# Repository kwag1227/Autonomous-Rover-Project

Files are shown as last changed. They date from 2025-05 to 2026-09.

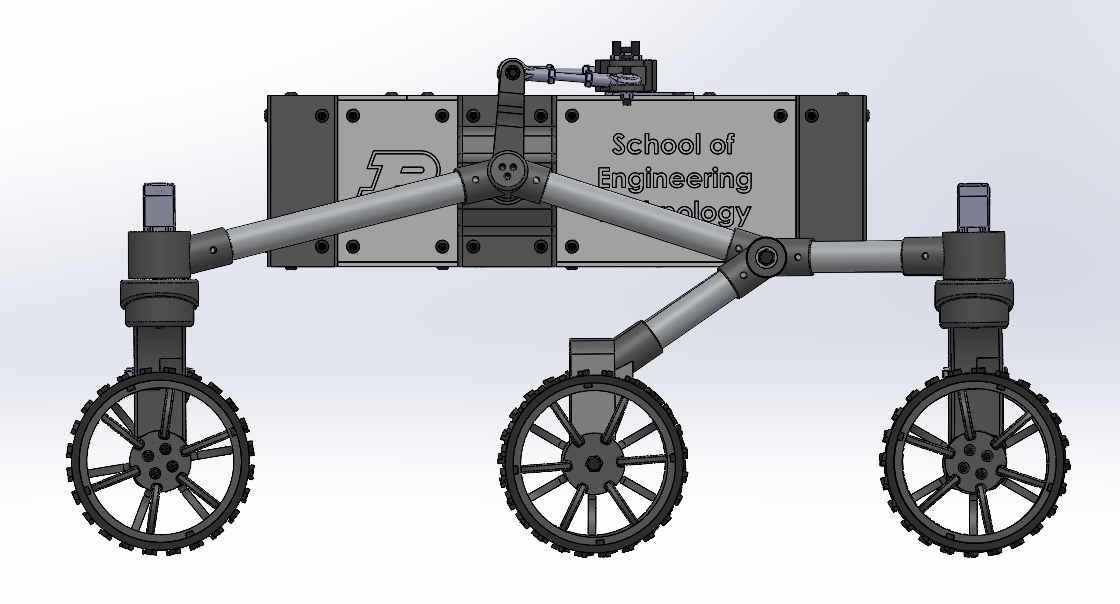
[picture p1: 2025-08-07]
mechanical designs/Screenshots/Screenshot 2025-08-07 133648.png

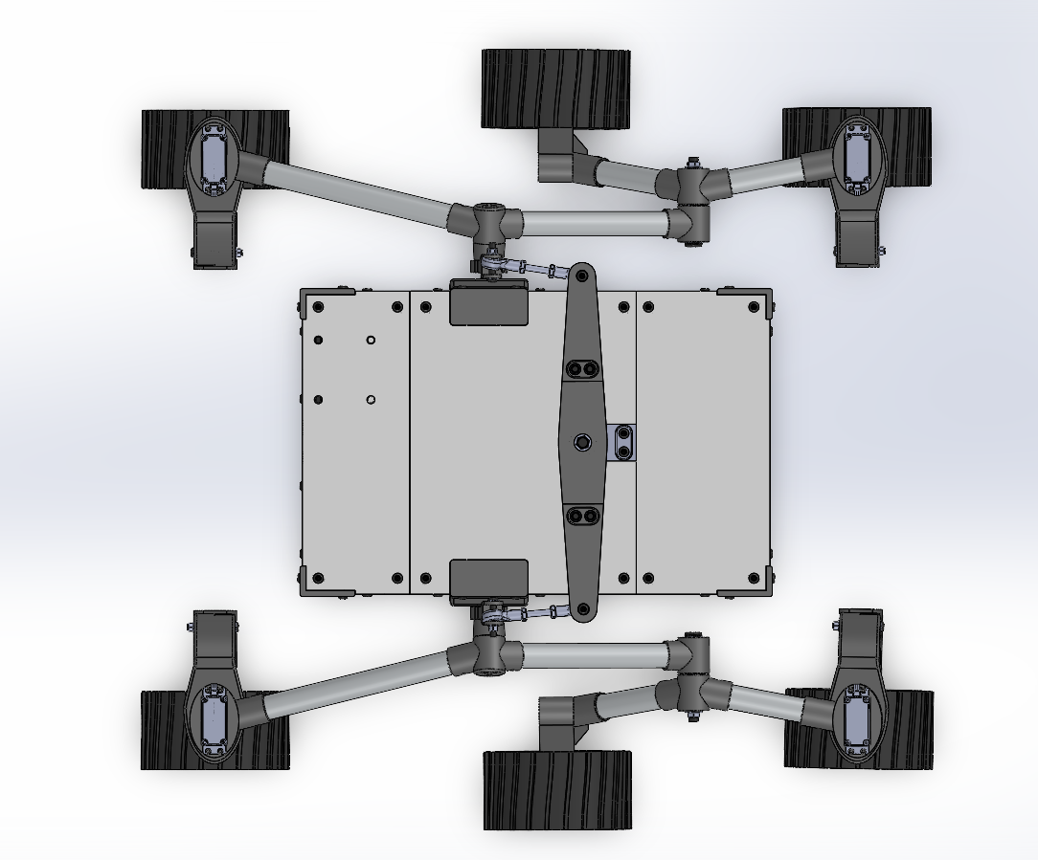
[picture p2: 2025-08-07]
mechanical designs/Screenshots/Screenshot 2025-08-07 133636.png

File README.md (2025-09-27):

# Autonomous Rover Project

This repository contains all design files, software, and documentation for an all-terrain, six-legged rover capable of navigating rough terrain and collecting environmental samples. It is a personal robotics project focused on demonstrating skills in embedded systems, motor control, and computer vision.

## 🚀 Project Goals

- Navigate difficult terrain using a rocker-bogie suspension system
- Collect and store small samples (e.g., rocks or soil)
- Avoid untraversable obstacles using sensors
- Showcase design and control of a multi-motor robotic system
- Build a custom PCB
- Implement ROS2 and Gazebo Simulation

## 📁 Repository Structure

- /code                       Microcontroller firmware and Raspberry Pi software  
- /mechanical design          CAD files & mechanical designs
- /electrical schematics      PCB schematics & electrical diagrams
- /vision                     Computer vision and object detection scripts  
- /docs                       Design notes and planning documents 
- /tests                      Testing scripts and logs  
- /media                      Images or videos of the rover in progress
- /references                 Reference images that I gathered from online
- /archives                   Outdated documents/files that are no longer in use
- README.md                   Project overview and documentation  

## 🧰 Technologies Used

- Raspberry Pi 4 (with OpenCV for computer vision)
- Raspberry Pi Pico
- Python Programming Language and ROS
- Rocker-Bogie Suspension System
- Camera Module
- Sensors (IMU, GPS, Encoders, Magnetometer)
- Custom PCB

## 🛠️ Current Progress

- [x] Preliminary Research
- [x] Conceptual Design
- [x] Power Distribution Design
- [x] Control/Communication Design
- [x] Master Electrical Schematic Design
- [x] PCB Design
- [x] CAD Design
- [x] Finalized BOM
- [x] Mechanical Assembly
- [ ] Electrical Assembly
- [ ] Basic Drive Logic
- [ ] Autonomy Logic
- [ ] Articulated Arm Design
- [ ] Articulation Logic 

## 📷 Media

*Add photos or videos here later*

## 🔒 Status

This is a personal project still under development

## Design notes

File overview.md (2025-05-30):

# All-Terrain Sampling Rover Project

## 1. Define Mission Requirements

### a. What is the goal?
The goal of this project is to create a rover-like robot that has similar functionality to real-life rovers used today, albeit on a much simpler scale. I plan to add to this project over time, learning about advanced features related to computer vision and robot navigation eventually.

### b. What are the operational constraints?

#### i. Mechanical:
- Collect 10mL sample and store
- Traversable across rocky/uneven terrain

#### ii. Electrical:
- Minimum runtime of 15 minutes
- Wireless operation
- Solar-rechargeable battery

#### iii. Software:
- Autonomous control – Finite State Machine
- Sensor feedback (IMU, Camera, Ultrasonic Sensor, Wheel Encoders)
- Decision-making based on I/O
- GPS tracking
- Implement ROS

---

## 2. Subsystem Breakdown

### a. Chassis
- **Purpose**: Houses majority of electronics and hardware, provides protection against outside elements  
- **Function**: Shield electronics, maintain upright position, hold inner contents securely  
- **Components**: Frame, housings, internal/external mounts  

### b. Drivetrain
- **Purpose**: High-torque system that allows for movement on steep inclines  
- **Function**: Forward/backward movement, differential drive, steering capability  
- **Components**: 4x Wheel motors (BLDC), high-grip wheels, leg assemblies, wire housing  

### c. Power System
- **Purpose**: Providing power to all components  
- **Function**: Voltage regulation, current protection, battery management, stepping down voltage for logic devices, on/off control  
- **Components**: Battery pack, on/off switch, 12V-to-5V buck converter, fuse/current limiter, ground bus, microcontroller breakout board, PCB board  

### d. Control
- **Purpose**: Managing I/O and coordinating robot functions  
- **Function**: Generating PWM signals, processing remote control inputs, managing sensor data, using logic to make decisions  
- **Components**: Main Controller (Raspberry Pi 3 – Arduino Mega doesn’t support camera), Drive ESCs, Articulated Arm Controller (Pi Pico)  

### e. Sensing
- **Purpose**: Measuring and recording data for decision-making  
- **Function**: Track robot position/orientation, detect obstacles, track state of sample collector  
- **Components**: Ultrasonic sensor, IMU, camera module, wheel encoders  

### f. Actuation
- **Purpose**: Controlling the sample-collecting device  
- **Function**: Using a 2–3 DOF articulated arm for scooping  
- **Components**: 1 main arm link, 3 servo motors (base rotation, shoulder hinge, wrist hinge – high torque), end effector (scooper)  

### g. Communications
- **Purpose**: Data transfer between subsystems  
- **Function**: Sensor/controller communication, command output, code uploading  
- **Components**: UART/I2C/SPI buses, USB/Ethernet (for code uploading)  

---

## 3. Performance Specs

### Chassis
- **Max weight capacity**: ≥ 18 lbs

### Drivetrain
- **Max obstacle height**: 150% of Wheel Diameter (6.75")
- **Minimum drive motor torque**: 17.7 in-lbs (2.0 N*m)

### Power System
- **Battery life**: ≥ 15 minutes continuous operation
- **Voltage rails**: 12V, 5V
- **Safety**: Include overcurrent protection and emergency shutoff

### Control
- **Latency (input to actuation)**: ≤ 100 ms
- **Redundancy**: Safe failure behavior if primary controller fails
- **Interface compatibility**: Must support all communication protocols

### Sensing
- **Obstacle detection range (ultrasonic)**: ≥ 5'
- **IMU update rate**: ≥ 100 Hz
- **Camera resolution**: ≥ 640x480 @ 30 fps
- **Sensor fusion accuracy**: ≤ ±5° orientation error

### Actuation (Sampler Device)
- **Reach**: ≥ 10" from arm base
- **Payload capacity**: ≥ 3lbs (soil or rock sample)
- **Servo torque**: Sufficient to operate at full arm extension under load
- **Repeatability**: ≤ 0.5" positioning error
- **Degrees of Freedom**: 3

### Communications
- **Internal latency (inter-microcontroller)**: ≤ 10 ms
- **Signal integrity**: Must operate reliably under EMI from motors
- **Wiring**: Clearly labeled, shielded where needed
- **Bandwidth**: Must support 30 fps camera feed to Pi 3
- **Protocol support**: WIFI UART, I2C, SPI, PWM

### Software
- **Error handling**: Subsystem-level watchdogs and fail-safe states
- **Modularity**: Software structured into independent modules for each subsystem
- **Real-time control loop**: ≥ 10 Hz for locomotion and sensing
- **Remote override**: Support for manual override during autonomous mode

---

## 4. Interfacing

### a. I2C
- **Benefits**: Only two wires to connect many components  
- **Usage**: Connecting sensors to the Pi  
- **Limitations**: Short-range, noise-prone, address conflicts, slow speed (not suitable for camera)  

### b. CSI
- **Benefits**: High data throughput, Pi-optimized, easy and power-efficient  
- **Usage**: Connecting camera module  
- **Limitations**: Limited number of ports, requires CSI-compatible camera  

### c. Wi-Fi
- **Usage**: Streaming camera feed/sensor data to laptop from Pi  

### d. PWM
- **Usage**: Controller output signal to ESCs and motors  

### e. UART
- **Benefits**: Only 2 lines, GPS-compatible, asynchronous  
- **Usage**: Communicating with GPS module  
- **Limitations**: One-to-one device connection, baud rate must match, code must read data quickly  

---

## 5. Documentation

- **BOM Link**: _[https://docs.google.com/spreadsheets/d/1kCPw5noG4wiGUhccGp7jNWA5f-jaydbZb4b8pzQ2dAw/edit?usp=sharing]_  
- **GitHub**: _[https://github.com/kwag1227/Autonomous-Rover-Project/tree/main]_  
- **YouTube Video Progress Reports**: _[Add playlist or links]_

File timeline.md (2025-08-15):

## Project Timeline

### Week 1 – Project Planning & Scoping
- Finalize project overview (mission, constraints, subsystems)
- Create early sketches of subsystems
- Set up documentation system (GitHub, folders)

### Week 2 – Conceptual Design
- Create master sketch with accurate dimensions
- Define conceptual control flow between sensors, logic, and motors
- Decide PCB responsibilities

### Week 3 – Detailed Design
- Finalize mechanical and control architecture
- Select core electrical components

### Week 4 – BOM Refinement & Electrical Schematics
- Swap general parts for specific parts
- Create power distribution PCB electrical schematic
- Create control PCB electrical schematic

### Week 5 – PCB Schematic Design
- Finish electrical components refinement
- Create KiCAD master electrical schematic for PCB
- Perform electronic rules check and address all errors/warnings

### Week 6 – PCB Layout Design
- Research PCB design principles
- Create PCB layout based off finalized electrical schematic
- Perform design rules check and address all errors/warnings

### Week 7 – Mechanical Design Kickoff
- Refine BOM for mechanical components
- Establish deadlines for mechanical subsystems
- Begin work on rover chassis

### Week 8 – Chassis Design + 3D Printer Order
- Order 3D Printer + Accessories
- Select 3D print materials for rover components
- Finish mechanical design of rover chassis

### Week 9 – Drivetrain Design & Filament Ordering
- Order all electrical components
- Design rocker-bogie drivetrain subsystem
- Set up 3D printer and order required filaments types

### Week 10 – CAD Finalization, Parts Ordering, Pi 4 Setup
- Finalize CAD model
- Order MCUs + accessories and PCB + components for soldering
- Set up Raspberry OS on Pi 4

### Week 11 – BOM Finalization, Software Setup & Training
- Finalize BOM with updated mechanical components
- Solder all PCB components
- Set up Pi Pico
- Install ROS2 and Gazebo software
- C++ and ROS2 Training

### Week 12 – Project Relocation / Transition Week
- Moving back to university, bring all required components and equipment
- Begin printing drivetrain components
- Order mechanical components if possible

### Week 13 & Beyond - Electrical and Mechanical Assembly
- Order/print all remaining components and assemble
- Finish internal/external wiring
- Begin writing ROS2 nodes for rover locomotion
- Create project overview video

### Future Additions - Advanced logic scripts + rover functionality
- Implement logic that handles all sensor data and provides live telemetry to off-board computer
- Create FSM-level autonomy logic.
- Begin implementing Gazebo simulation
- Design and implement 3-axis robotic arm for sample gathering
- Finish 2-DOF camera mount design
- Consider future additions (actuated camera head, SLAM computer vision, & sample storage)

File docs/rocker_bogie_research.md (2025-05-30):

# Rocker-Bogie Drivetrain Research

## Overview
Below is notes taken regarding the rocker-bogie suspension system that will be used for this project. 
This is a preliminary document intended for future reference during the design phase.
Created on 5/20/25

## Mechanical Design
- 3 Main Components:
    1. Differential - Pivot point about center of chassis, connects left and right rockers to the rover body. Acts as a counter-balancing mechanism (one rocker goes up, the other goes down), keeping the chassis more level and all wheels in contact with the ground. Can be done using bevel gears, but NASA opts for a pivoting mechanical linkage, which reduces points of failure.
    2. Rocker - Main joint that connects the front wheel to the bogie. The rocker linkage connector is fastened to the joint hub, and the joint hub rotates around a fixed shaft protruding from the chassis. See reference images for joint hub design.
    3. Bogie - Secondary rocker that connects the middle and back wheels together.
- This design provides fully passive stability, there are no springs that maintain a default position.

## Kinematics & Geometry
- For both the rocker and bogie, the links on each side are the same length. This means that the middle wheels are shifted closer to the back wheels than to the front wheel.
- Wheels can traverse obstacles 1.5-2 * wheel diameter
- Can handle 45 degree tilt in any direction
- Front and back wheels are aligned, middle wheels stick out about half a wheel more

## Materials and Components
- All of the weight of the rocker-bogie suspension will be on the rocker joint hub components, which should be made of a stronger material.
- All components are stiff and a fixed size besides the wheel tread, which should be slightly pliable and have a tread pattern of simple horizontal lines.

## Design Considerations for My Rover
- I should probably use the same differential system used by NASA, which will be easier to 3d print. An additional linkage is required on each side with this version. This linkage is connected via two pinned joints, allowing for the linkage to remain forward-facing despite the transverse-plane rotation of the differential bar and sagittal-plane rotation of the rocker joint hub.
- While NASA utilizes four steering motors (one for each corner), I only need to use two for the front two wheels. Use Ackermann steering calculations to independently control the angle of each wheel during a turn. Include motor hubs for back wheels in case want more manuevarability in future.
- The sides are mirrors of each other, don't make them identical.
- The rocker joint component, on which the rocker linkage connection is fastened, is tilted slightly upwards, which is what allows for the linkages to go outwards at an angle, rather than being straight up and down.
- Dimensions (given in mm) have been uploaded to reference images folder, decide what scale you want to use for this and convert values from there. Keep in mind that the values used in the the reference image dimensions are not the same scale as the real rover, but they are proportionally accurate.
- Make sure that the rocker joint 3d-printed component is printed with the layers travelling along the shaft that the links are fastened too. That area us under the most stress due to it holding the full weight of the chassis.

## References
NASA JPL Youtube Video - https://www.youtube.com/watch?v=BC441bV1wFc
NASA Website Perserverance Rover Breakdown - https://science.nasa.gov/mission/mars-2020-perseverance/rover-components/
DIY Rover Youtube Video - https://www.youtube.com/watch?v=NOZZMsMAGh0&t=1s
NASA-provided 3D Model - https://science.nasa.gov/resource/mars-perseverance-rover-3d-model/
Check reference images folder

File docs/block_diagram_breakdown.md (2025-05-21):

# Autonomous Rover Project – High-Level System Block Diagram

## 📦 Subsystem Breakdown

### 1. Chassis
**Components:**
- Frame
- Top and bottom plates
- Side plates
- Front and back plates
- Battery housing
- Internal/external mounts

---

### 2. Drivetrain
**Components:**
- 4x BLDC drive motors
- 2x High-torque servo motors (for steering)
- High-grip, flexible wheels
- Wheel hubs
- Rocker-bogie assembly
- Differential bar assembly

---

### 3. Power System
**Components:**
- LiPo battery
- Battery connector (XT90)
- DC On/off switch
- 12V-5V Buck converter
- Screw terminals
- Fuse/breaker
- Ground bus
- Power PCB board
- Wire hose
- Zip ties

---

### 4. Control
**Components:**
- Main Controller: Raspberry Pi 3
- Robot Controller: Raspberry Pi Pico
- Main PCB Board
- Drive ESCs
- GPIO headers

---

### 5. Sensing
**Components:**
- Ultrasonic sensor
- IMU
- Camera module
- Wheel encoders
- Limit switches? (for arm)
- GPS?

---

### 6. Actuation 
**Components:**
- Main arm link
- Shoulder joint hub
- Wrist joint hub
- End effector (scooper)
- 3x Additional high-torque servo motors (shoulder rotation, shoulder hinge, wrist hinge)

---

### 7. Communications
**Components:**
- UART bus wiring/connectors
- UART twisted wire cables (TX+gnd, RX+gnd)
- I2C bus wiring/connectors
- I2C twisted wire cables (SDA+gnd, SCL+gnd)
- I2C pull-up resistors (For SDA and SCL lines)
- CSI ribbon cable
- PWM wires

---

## 🖼️ Block Diagram

**Diagram Filename:** `Rover Block Diagram.png`

_Description:_  
This diagram illustrates the connections and dependencies between all major subsystems, including power distribution, sensory input, decision-making, and actuation systems.

---

## 📌 Notes & Future Considerations

- Consider adding solar recharging or power monitoring sensors.
- Possible integration of SLAM or GPS for autonomous mapping in the future.
- Expand sensing array with LIDAR or stereo vision for better 3D awareness.

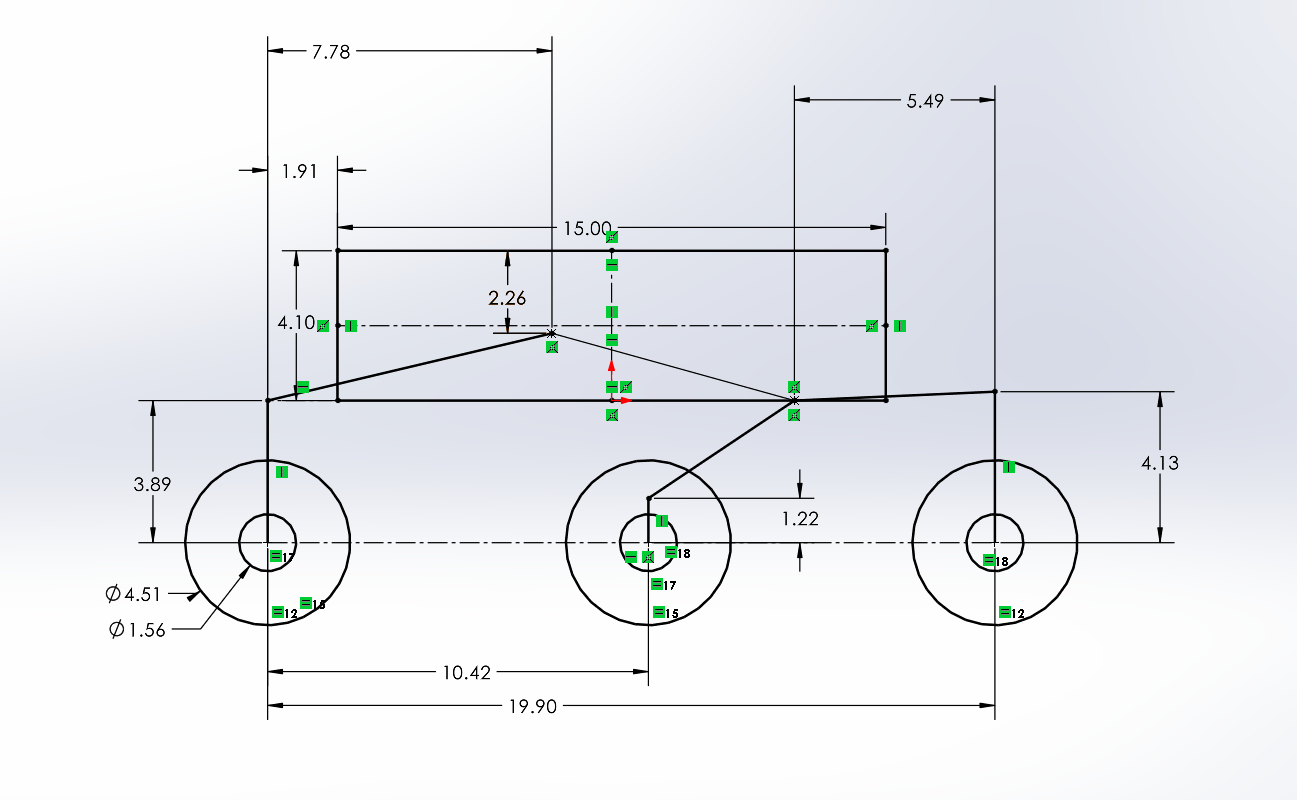
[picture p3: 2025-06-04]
mechanical designs/Screenshots/Master Sketch Side View Screenshot.png

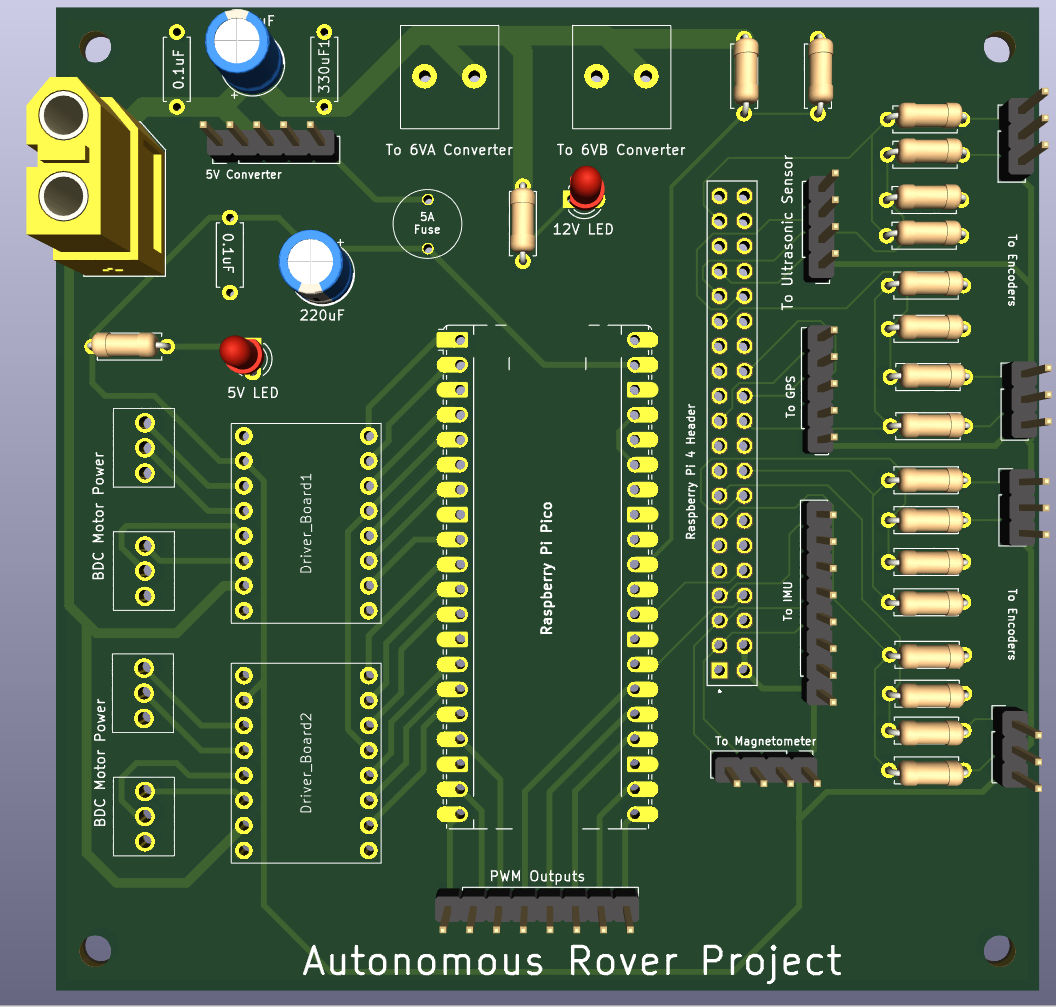
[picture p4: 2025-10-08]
electrical schematics/PCB 3D Viewer.png

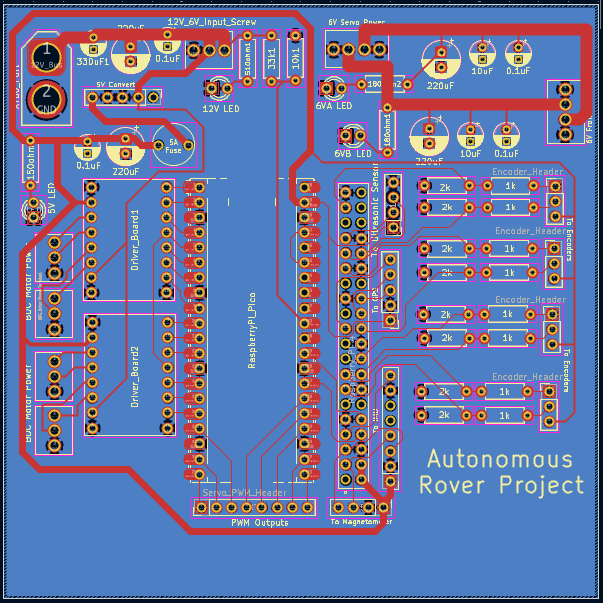
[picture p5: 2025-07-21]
electrical schematics/Finalized PCB Layout.png

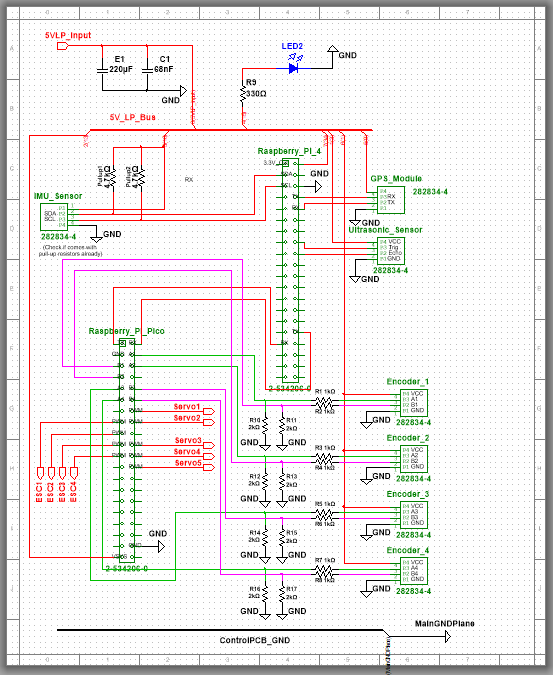
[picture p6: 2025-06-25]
electrical schematics/Control Schematic Screenshot.png

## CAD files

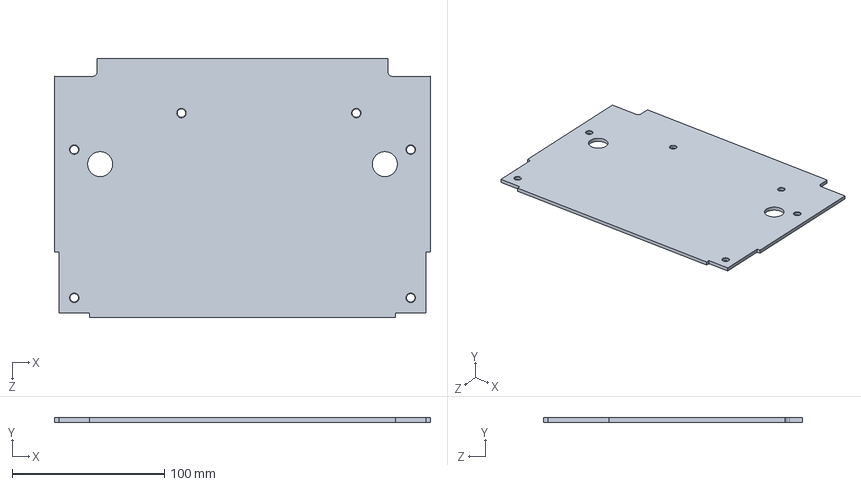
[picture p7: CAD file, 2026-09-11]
mechanical designs/Chassis/Top_Bottom_Panels.SLDPRT
247.3 x 3.00 x 170.5 mm

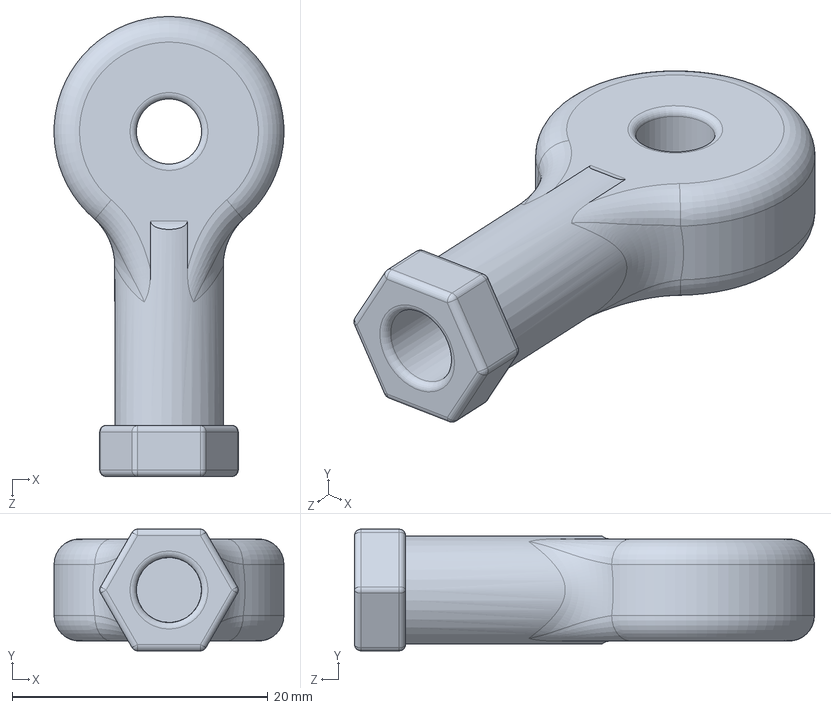
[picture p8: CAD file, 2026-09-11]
mechanical designs/Fasteners & Power Transmission/Heim Joint/Hiem Joint Socket.SLDPRT
18.0 x 9.53 x 36.0 mm

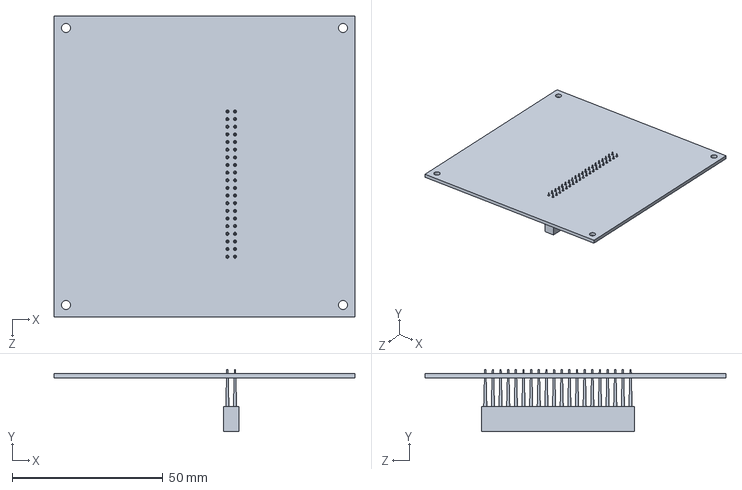
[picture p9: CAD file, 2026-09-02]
mechanical designs/Internal Electronics/PCB.SLDPRT
100.0 x 20.7 x 100.0 mm

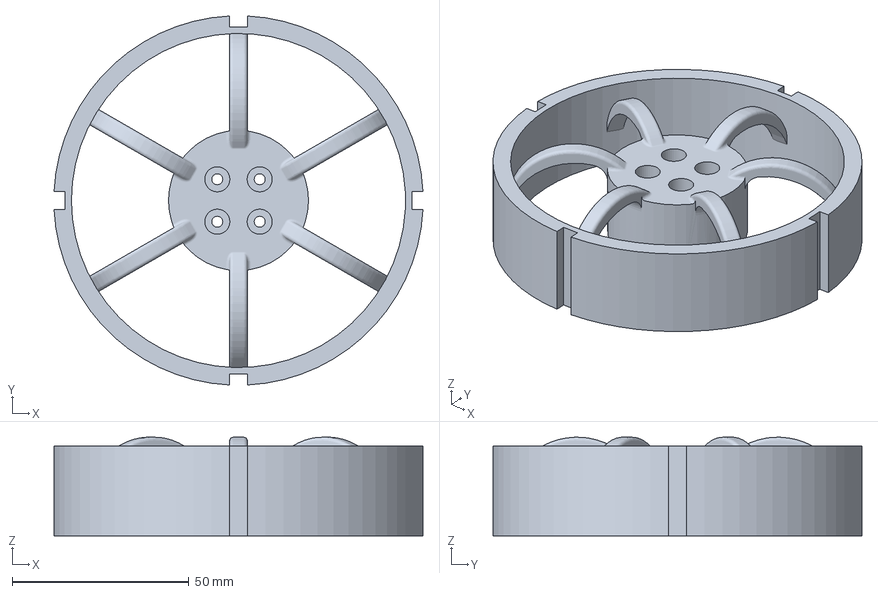
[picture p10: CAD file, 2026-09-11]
mechanical designs/Print Files/PETG White/Outer Wheel Hub.3mf
104.4 x 104.4 x 27.9 mm

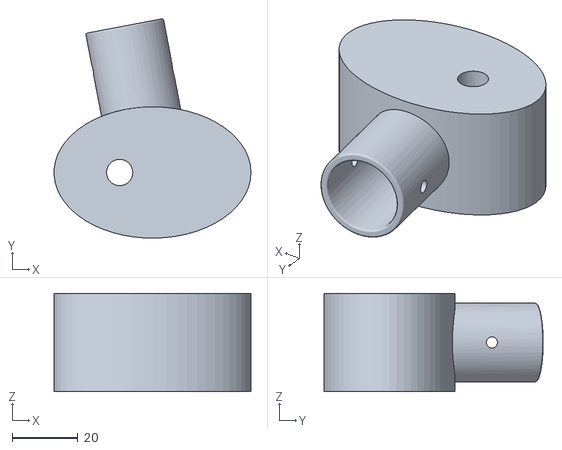
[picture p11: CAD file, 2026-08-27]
mechanical designs/Print Files/PETG-CF Gray/Steering Motor Housing Back Left.STL
60.0 x 66.8 x 30.0

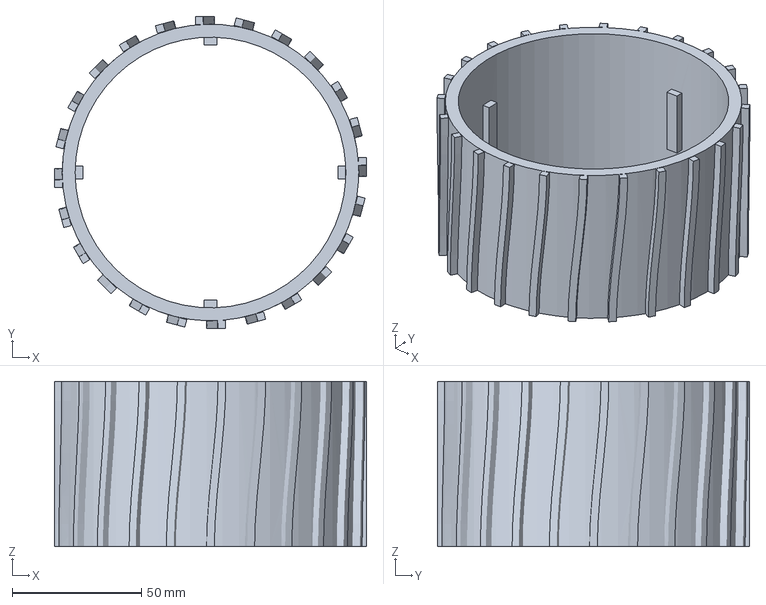
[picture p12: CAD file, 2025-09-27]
mechanical designs/Print Files/TPU 95A Black/Tires.3mf
120.5 x 120.5 x 63.8 mm

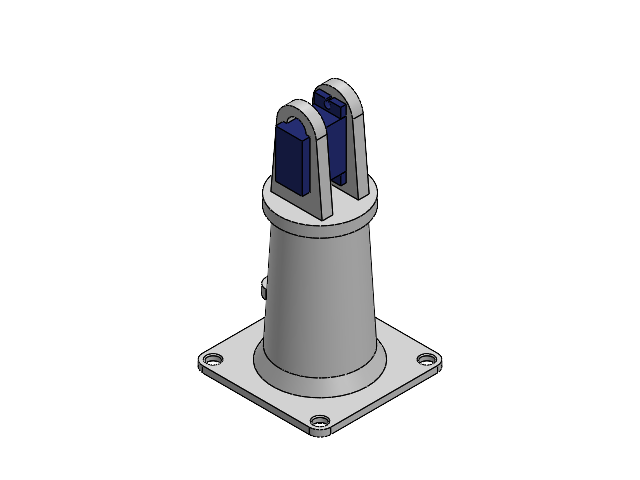
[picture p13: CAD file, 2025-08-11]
mechanical designs/Camera Head/Camera Mount Subassembly.SLDASM
Component1.step x 2
Component2.step x 2
Component3.step x 2
Component4.step x 2
Component5.step x 2
Component6.step x 2
Servo Shaft Coupler
Threaded Rod
Pitch Servo Mount
Camera Mount Base

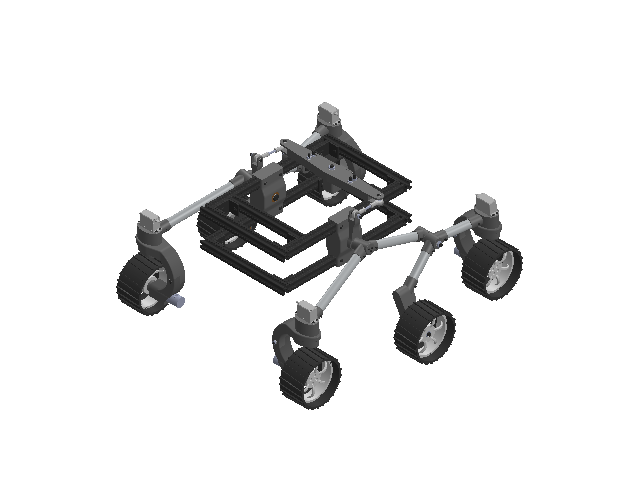
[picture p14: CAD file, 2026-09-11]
mechanical designs/Drivetrain/Drivetrain Subassembly.SLDASM
T-Slot_Extrusions x 10
T-Slot_Nut x 44
Threaded_Bolts x 149
T-Slot_Corner_Bracket x 12
Rocker_Joint_Mounting_Plate x 2
Ball_Bearing x 12
Differential_Mount
Differential Center Piece
Washers x 37
Nuts x 19
Differential Outer Piece x 2
Threaded Rods x 2
Rocker Joint Hub x 2
Hiem Joint Socket x 4
Hiem Joint Bearing x 4
Threaded Insert x 46
Rocker Joint x 2
20mm Aluminum Tubes x 8
Bogie Components x 4
SW2019 DS3225MG Servo 25Kg 4.8-6.8V x 4
Servo Horn x 4
Steering Motor Housing x 3
Steering Linkage x 4
Drive Motor x 4
Drive Motor Housing x 4
Middle Wheel Hub x 2
Drive Motor Shaft Coupler x 4
Wheel Hub x 6
Tires x 6

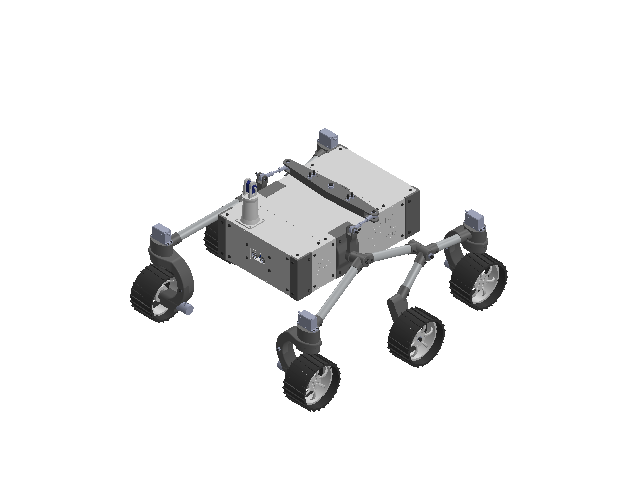
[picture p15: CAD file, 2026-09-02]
mechanical designs/Top Level Assembly.SLDASM
T-Slot_Extrusions x 10
T-Slot_Nut x 104
Threaded_Bolts x 221
T-Slot_Corner_Bracket x 12
Rocker_Joint_Mounting_Plate x 2
Ball_Bearing x 12
Chassis_Corner_Panel x 4
Side_Panels x 4
ultrasonic sensor_3.step
Ultrasonic_Sensor_Bracket
Chassis_Front_Panel x 2
Nuts x 23
Differential_Mount
Top_Bottom_Panels x 5
Battery
PCB, RPi4ModelB.step
Broadcom BCM2711B0 CPU, RPi4ModelB.step
2.54 mm DUPONT MALE PIN HEADER, POE, 2X2, RPi4ModelB.step
2.54 mm DUPONT MALE PIN HEADER, IO, 2X20, RPi4ModelB.step
Camera Connector, RPi4ModelB.step
Microphone Plug, RPi4ModelB.step
Display Connector, RPi4ModelB.step
Gigabit Ethernet Port, RPi4ModelB.step
Female Micro HDMI Connector, RPi4ModelB.step x 2
Female USB Type C Connector, RPi4ModelB.step
2X USB3.0 PORTS, RPi4ModelB.step
91D77 D9WHV 778K, 4 GB LPDDR4 SDRAM, RPi4ModelB.step
Cypress CYW43455 Wireless Module Cover, RPi4ModelB.step
SD Card Slot, RPi4ModelB.step
VIA VL805 PCIe USB 3.0 controller, RPi4ModelB.step
2X USB2.0 PORTS, RPi4ModelB.step
Broadcom BCM54213PE Gigabit Ethernet Transceiver, RPi4ModelB.step
MxL7704 Universal PMIC, RPi4ModelB.step
PCB
MCU-PCB Mounting Plate^MCU-PCB Mounting Plate
Differential Center Piece
Washers x 42
Differential Outer Piece x 2
Threaded Rods x 2
Rocker Joint Hub x 2
Hiem Joint Socket x 4
Hiem Joint Bearing x 4
Threaded Insert x 30
Rocker Joint x 2
20mm Aluminum Tubes x 8
Bogie Components x 4
SW2019 DS3225MG Servo 25Kg 4.8-6.8V x 4
Servo Horn x 4
Servo Horn Coupler x 4
Steering Motor Housing
Steering Linkage x 4
Drive Motor x 4
Drive Motor Housing x 4
Middle Wheel Hub x 2
Drive Motor Shaft Coupler x 4
Wheel Hub x 6
Tires x 6
Component1.step x 2
Component2.step x 2
Component3.step x 2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

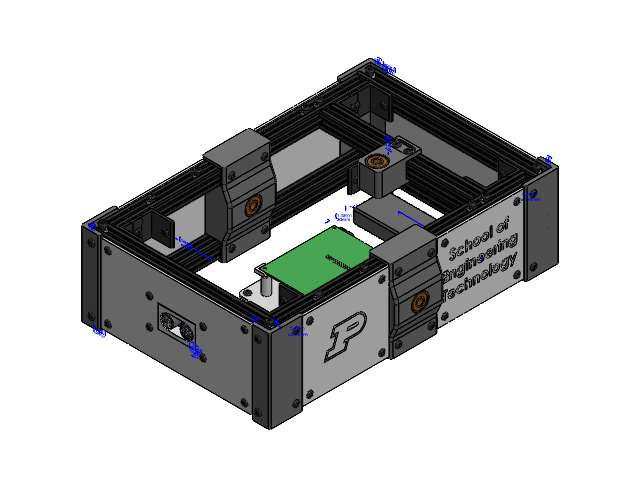
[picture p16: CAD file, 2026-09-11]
mechanical designs/Chassis/Chassis_Subassembly.SLDASM
T-Slot_Extrusions x 9
T-Slot_Nut x 104
Threaded_Bolts x 116
T-Slot_Corner_Bracket x 12
Rocker_Joint_Mounting_Plate x 2
Ball_Bearing x 6
Chassis_Corner_Panel x 4
Side_Panels x 4
ultrasonic sensor_3.step
Ultrasonic_Sensor_Bracket
Chassis_Front_Panel x 2
Nuts x 8
Differential_Mount
Battery
PCB, RPi4ModelB.step
Broadcom BCM2711B0 CPU, RPi4ModelB.step
2.54 mm DUPONT MALE PIN HEADER, POE, 2X2, RPi4ModelB.step
2.54 mm DUPONT MALE PIN HEADER, IO, 2X20, RPi4ModelB.step
Camera Connector, RPi4ModelB.step
Microphone Plug, RPi4ModelB.step
Display Connector, RPi4ModelB.step
Gigabit Ethernet Port, RPi4ModelB.step
Female Micro HDMI Connector, RPi4ModelB.step x 2
Female USB Type C Connector, RPi4ModelB.step
2X USB3.0 PORTS, RPi4ModelB.step
91D77 D9WHV 778K, 4 GB LPDDR4 SDRAM, RPi4ModelB.step
Cypress CYW43455 Wireless Module Cover, RPi4ModelB.step
SD Card Slot, RPi4ModelB.step
VIA VL805 PCIe USB 3.0 controller, RPi4ModelB.step
2X USB2.0 PORTS, RPi4ModelB.step
Broadcom BCM54213PE Gigabit Ethernet Transceiver, RPi4ModelB.step
MxL7704 Universal PMIC, RPi4ModelB.step
PCB
MCU-PCB Mounting Plate^MCU-PCB Mounting Plate

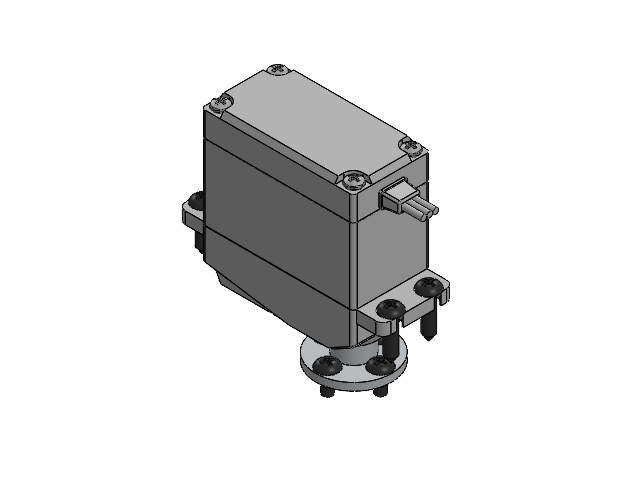
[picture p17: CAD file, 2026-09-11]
mechanical designs/Drivetrain/Steering Motor Mount.SLDASM
SW2019 DS3225MG Servo 25Kg 4.8-6.8V
Servo Horn
Threaded_Bolts x 8

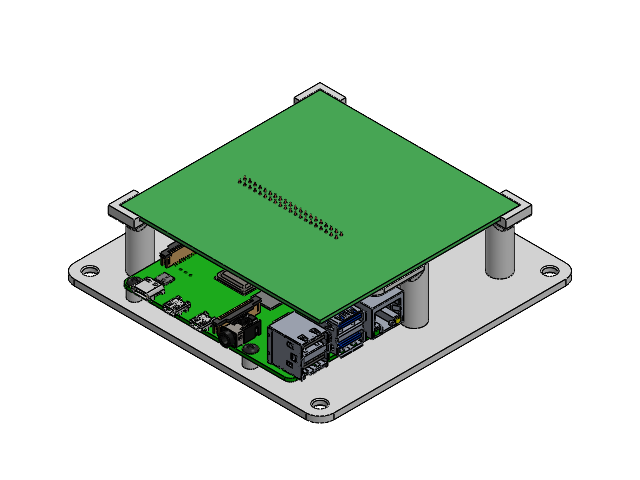
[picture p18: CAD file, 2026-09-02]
mechanical designs/Internal Electronics/MCU-PCB Mounting Plate.SLDASM
PCB, RPi4ModelB.step
Broadcom BCM2711B0 CPU, RPi4ModelB.step
2.54 mm DUPONT MALE PIN HEADER, POE, 2X2, RPi4ModelB.step
2.54 mm DUPONT MALE PIN HEADER, IO, 2X20, RPi4ModelB.step
Camera Connector, RPi4ModelB.step
Microphone Plug, RPi4ModelB.step
Display Connector, RPi4ModelB.step
Gigabit Ethernet Port, RPi4ModelB.step
Female Micro HDMI Connector, RPi4ModelB.step x 2
Female USB Type C Connector, RPi4ModelB.step
2X USB3.0 PORTS, RPi4ModelB.step
91D77 D9WHV 778K, 4 GB LPDDR4 SDRAM, RPi4ModelB.step
Cypress CYW43455 Wireless Module Cover, RPi4ModelB.step
SD Card Slot, RPi4ModelB.step
VIA VL805 PCIe USB 3.0 controller, RPi4ModelB.step
2X USB2.0 PORTS, RPi4ModelB.step
Broadcom BCM54213PE Gigabit Ethernet Transceiver, RPi4ModelB.step
MxL7704 Universal PMIC, RPi4ModelB.step
PCB
MCU-PCB Mounting Plate^MCU-PCB Mounting Plate
Threaded_Bolts x 4

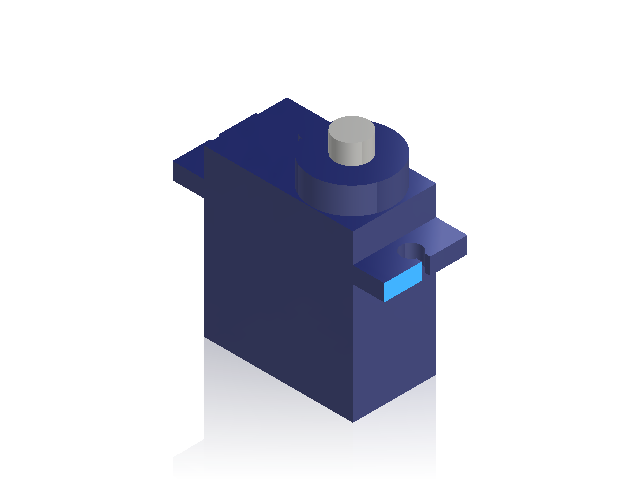
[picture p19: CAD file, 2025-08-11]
mechanical designs/Camera Head/SG90 Servo Beffkipp.SLDASM
Component1.step
Component2.step
Component3.step
Component4.step
Component5.step
Component6.step

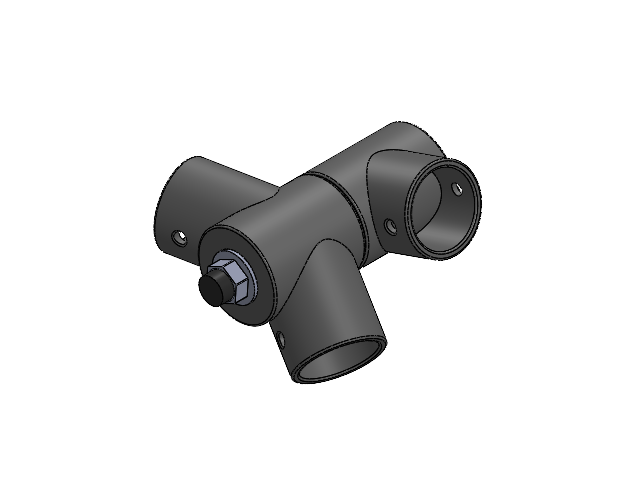
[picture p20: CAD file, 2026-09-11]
mechanical designs/Drivetrain/Bogie Joint.SLDASM
Ball_Bearing x 2
Nuts
Threaded_Bolts
Washers x 3
Bogie Components x 2

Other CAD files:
mechanical designs/Fasteners & Power Transmission/Heim Joint/Female Heim Joint.SLDASM
mechanical designs/Chassis/Corner_Bracket_Subassembly.SLDASM
mechanical designs/Drivetrain/Drive Motor Joint.SLDASM
mechanical designs/Drivetrain/Wheel Assembly.SLDASM
mechanical designs/Camera Head/Camera Mount Base.SLDPRT
mechanical designs/Camera Head/Pitch Servo Mount.SLDPRT
mechanical designs/Camera Head/Servo Shaft Coupler.SLDPRT
mechanical designs/Camera Head/Threaded Rod.SLDPRT
mechanical designs/Chassis/Chassis_Corner_Panel.SLDPRT
mechanical designs/Chassis/Chassis_Front_Panel.SLDPRT
mechanical designs/Chassis/Differential_Mount.SLDPRT
mechanical designs/Chassis/Rocker_Joint_Mounting_Plate.SLDPRT
mechanical designs/Chassis/Side_Panels.SLDPRT
mechanical designs/Chassis/T-Slot_Extrusions.SLDPRT
mechanical designs/Chassis/Ultrasonic_Sensor_Bracket.SLDPRT
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

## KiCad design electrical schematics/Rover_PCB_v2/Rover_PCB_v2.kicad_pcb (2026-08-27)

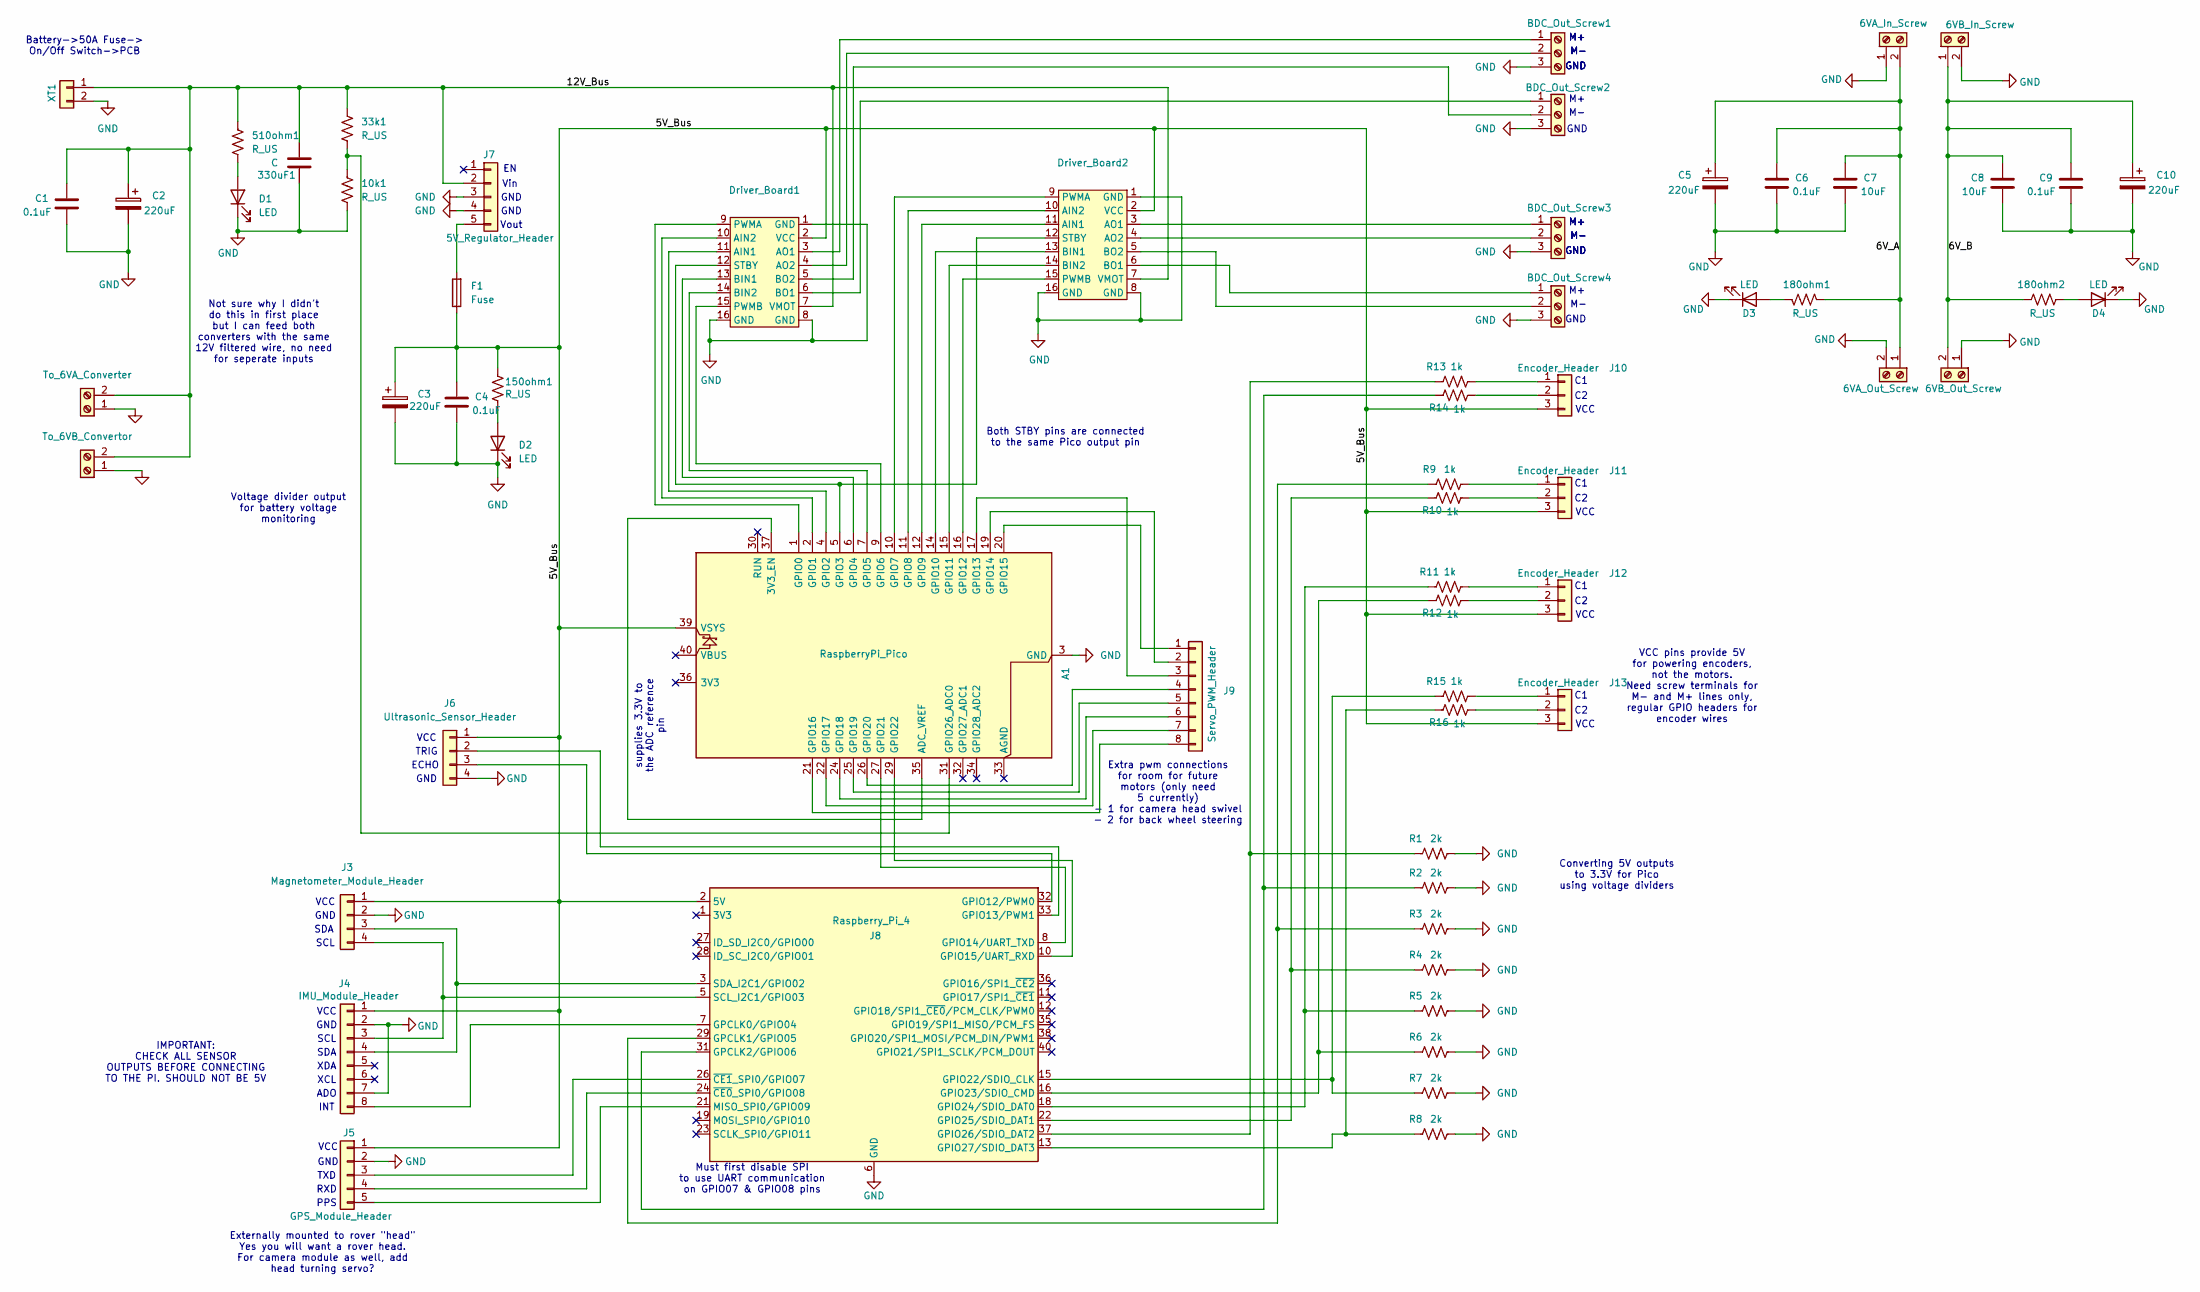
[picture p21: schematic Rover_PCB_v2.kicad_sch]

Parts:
10k1, 33k1, 150ohm1, 180ohm1, 180ohm2, 510ohm1: R_US; R_Axial_DIN0207_L6.3mm_D2.5mm_P7.62mm_Horizontal
330uF1: C; CP_Radial_D4.0mm_P2.00mm
A1: RaspberryPi_Pico; RaspberryPi_Pico_Common_Unspecified
BDC_Out_Screw1, BDC_Out_Screw2, BDC_Out_Screw3, BDC_Out_Screw4: BDC_Motor_Screw_Terminal; 01x03_Screw_Terminal
C1, C4, C6, C9: 0.1uF; CP_Radial_D4.0mm_P2.00mm
C2, C3, C5, C10: 220uF; CP_Radial_D6.3mm_P2.50mm
C7, C8: 10uF; CP_Radial_D4.0mm_P2.00mm
D1, D2, D3, D4: LED; LED_D3.0mm
Driver_Board1, Driver_Board2: Motor Driver Board
F1: Fuse; Fuse_TH_5A
J1: To_6VA_Converter; 12AWG Screw Terminal
J2: To_6VB_Convertor; 12AWG Screw Terminal
J3: Magnetometer_Module_Header; PinHeader_1x04_P2.54mm_Vertical
J4: IMU_Module_Header; PinHeader_1x08_P2.54mm_Vertical
J5: GPS_Module_Header; PinHeader_1x05_P2.54mm_Vertical
J6: Ultrasonic_Sensor_Header; PinHeader_1x04_P2.54mm_Vertical
J7: 5V_Regulator_Header; PinHeader_1x05_P2.54mm_Vertical
J8: Raspberry_Pi_4; SULLINS_PPTC202LFBN-RC
J9: Servo_PWM_Header; PinHeader_1x08_P2.54mm_Vertical
J10, J11, J12, J13: Encoder_Header; PinHeader_1x03_P2.54mm_Vertical
J14: 6VA_In_Screw; 12AWG Screw Terminal
J15: 6VA_Out_Screw; 12AWG Screw Terminal
J16: 6VB_In_Screw; 12AWG Screw Terminal
J17: 6VB_Out_Screw; 12AWG Screw Terminal
R1, R2, R3, R4, R5, R6, R7, R8: 2k; R_Axial_DIN0207_L6.3mm_D2.5mm_P7.62mm_Horizontal
R9, R10, R11, R12, R13, R14, R15, R16: 1k; R_Axial_DIN0207_L6.3mm_D2.5mm_P7.62mm_Horizontal
XT1: XT60_Port; AMASS_XT60-F_1x02_P7.20mm_Vertical

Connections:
/5V_Bus: 150ohm1.1, A1.39 (VSYS), C3.1, C4.1, Driver_Board1.2 (VCC), Driver_Board2.2 (VCC), F1.1, J3.1 (VCC), J4.1, J5.1 (VCC), J6.1 (VCC), J8.2 (5V), J8.4 (5V), J10.3 (VCC), J11.3 (VCC), J12.3 (VCC), J13.3 (VCC)
/6V_A: 180ohm1.1, C5.1, C6.1, C7.1, J14.2, J15.1
/6V_B: 180ohm2.1, C8.1, C9.1, C10.1, J16.1, J17.2
/12V_Bus: 33k1.2, 330uF1.1, 510ohm1.1, C1.1, C2.1, Driver_Board1.7 (VMOT), Driver_Board2.7 (VMOT), J1.2, J2.2, J7.2 (Vin), XT1.1 (12V_raw); also elsewhere on the board
GND: 10k1.2, 330uF1.2, A1.3 (GND), A1.8 (GND), A1.13 (GND), A1.18 (GND), A1.23 (GND), A1.28 (GND), A1.38 (GND), BDC_Out_Screw1.3 (GND), BDC_Out_Screw2.3 (GND), BDC_Out_Screw3.3 (GND), BDC_Out_Screw4.3 (GND), C1.2, C2.2, C3.2, C4.2, C5.2, C6.2, C7.2, C8.2, C9.2, C10.2, D1.2 (K), D2.2 (K), D3.2 (K), D4.2 (K), Driver_Board1.1 (GND), Driver_Board1.8 (GND), Driver_Board1.16 (GND), Driver_Board2.1 (GND), Driver_Board2.8 (GND), Driver_Board2.16 (GND), J1.1, J2.1, J3.2 (GND), J4.2, J4.7, J5.2 (GND), J6.4 (GND), J7.3 (GND), J7.4 (GND), J8.6 (GND), J8.9 (GND), J8.14 (GND), J8.20 (GND), J8.25 (GND), J8.30 (GND), J8.34 (GND), J8.39 (GND), J14.1, J15.2, J16.2, J17.1, R1.2, R2.2, R3.2, R4.2, R5.2, R6.2, R7.2, R8.2, XT1.2 (GND); also elsewhere on the board
unnamed: A1.35 (ADC_VREF), A1.37 (3V3_EN)
unnamed: A1.1 (GPIO0), Driver_Board1.9 (PWMA)
unnamed: A1.2 (GPIO1), Driver_Board1.10 (AIN2)
unnamed: A1.4 (GPIO2), Driver_Board1.11 (AIN1)
unnamed: A1.5 (GPIO3), Driver_Board1.12 (STBY), Driver_Board2.12 (STBY)
unnamed: A1.6 (GPIO4), Driver_Board1.13 (BIN1)
unnamed: A1.7 (GPIO5), Driver_Board1.14 (BIN2)
unnamed: A1.9 (GPIO6), Driver_Board1.15 (PWMB)
unnamed: A1.10 (GPIO7), Driver_Board2.9 (PWMA)
unnamed: A1.11 (GPIO8), Driver_Board2.10 (AIN2)
unnamed: A1.12 (GPIO9), Driver_Board2.11 (AIN1)
unnamed: A1.14 (GPIO10), Driver_Board2.13 (BIN1)
unnamed: A1.15 (GPIO11), Driver_Board2.14 (BIN2)
unnamed: A1.16 (GPIO12), Driver_Board2.15 (PWMB)
unnamed: A1.17 (GPIO13), J9.3
unnamed: A1.19 (GPIO14), J9.2
unnamed: A1.20 (GPIO15), J9.1
unnamed: A1.21 (GPIO16), J9.8
unnamed: A1.22 (GPIO17), J9.7
unnamed: A1.24 (GPIO18), J9.6
unnamed: A1.25 (GPIO19), J9.5
unnamed: A1.26 (GPIO20), J9.4
unnamed: A1.27 (GPIO21), J8.8 (GPIO14/UART_TXD)
unnamed: A1.29 (GPIO22), J8.10 (GPIO15/UART_RXD)
unnamed: 10k1.1, 33k1.1, A1.31 (GPIO26_ADC0)
unnamed 30: BDC_Out_Screw1.1 (M+), Driver_Board1.3 (AO1); also elsewhere on the board
unnamed 31: BDC_Out_Screw1.2 (M-), Driver_Board1.4 (AO2); also elsewhere on the board
unnamed: BDC_Out_Screw2.1 (M+), Driver_Board1.6 (BO1)
unnamed: BDC_Out_Screw2.2 (M-), Driver_Board1.5 (BO2)
unnamed: BDC_Out_Screw3.1 (M+), Driver_Board2.3 (AO1)
unnamed: BDC_Out_Screw3.2 (M-), Driver_Board2.4 (AO2)
unnamed: BDC_Out_Screw4.1 (M+), Driver_Board2.6 (BO1)
unnamed: BDC_Out_Screw4.2 (M-), Driver_Board2.5 (BO2)
unnamed: 510ohm1.2, D1.1 (A)
unnamed: 150ohm1.2, D2.1 (A)
unnamed: 180ohm1.2, D3.1 (A)
unnamed: 180ohm2.2, D4.1 (A)
unnamed: J3.4 (SCL), J4.3, J8.5 (SCL_I2C1/GPIO03)
unnamed: J3.3 (SDA), J4.4, J8.3 (SDA_I2C1/GPIO02)
unnamed: J4.8, J8.7 (GPCLK0/GPIO04)
unnamed: J5.5 (PPS), J8.21 (MISO_SPI0/GPIO09)
unnamed: J5.4 (RXD), J8.24 (~CE0_SPI0/GPIO08)
unnamed: J5.3 (TXD), J8.26 (~CE1_SPI0/GPIO07)
unnamed: J6.3 (Echo), J8.32 (GPIO12/PWM0)
unnamed: J6.2 (Trig), J8.33 (GPIO13/PWM1)
unnamed: F1.2, J7.5 (Vout)
unnamed: J8.29 (GPCLK1/GPIO05), R3.1, R9.1
unnamed: J8.31 (GPCLK2/GPIO06), R2.1, R14.1
unnamed: J8.15 (GPIO22/SDIO_CLK), R7.1, R15.1
unnamed: J8.16 (GPIO23/SDIO_CMD), R6.1, R12.1
unnamed: J8.18 (GPIO24/SDIO_DAT0), R5.1, R11.1
unnamed: J8.22 (GPIO25/SDIO_DAT1), R4.1, R10.1
unnamed: J8.37 (GPIO26/SDIO_DAT2), R1.1, R13.1
unnamed: J8.13 (GPIO27/SDIO_DAT3), R8.1, R16.1
unnamed: J10.1 (C1), R13.2
unnamed: J10.2 (C2), R14.2
unnamed: J11.1 (C1), R9.2
unnamed: J11.2 (C2), R10.2
unnamed: J12.1 (C1), R11.2
unnamed: J12.2 (C2), R12.2
unnamed: J13.1 (C1), R15.2
unnamed: J13.2 (C2), R16.2

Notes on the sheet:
GND
INT
Externally mounted to rover "head" Yes you will want a rover head. For camera module as well, add head turning servo?
GND
TRIG
VCC
Vin
SDA
SCL
supplies 3.3V to the ADC reference pin
TXD
Voltage divider output for battery voltage monitoring
XCL
Battery->50A Fuse-> On/Off Switch->PCB
IMPORTANT: CHECK ALL SENSOR OUTPUTS BEFORE CONNECTING TO THE PI. SHOULD NOT BE 5V
RXD
VCC pins provide 5V for powering encoders, not the motors. Need screw terminals for M- and M+ lines only, regular GPIO headers for encoder wires
Vout
ECHO
PPS
Both STBY pins are connected to the same Pico output pin
Not sure why I didn't do this in first place but I can feed both converters with the same 12V filtered wire, no need for seperate inputs
XDA
Must first disable SPI to use UART communication on GPIO07 & GPIO08 pins
Extra pwm connections for room for future motors (only need 5 currently) - 1 for camera head swivel - 2 for back wheel steering
ADO
Converting 5V outputs to 3.3V for Pico using voltage dividers

Board: 2 copper layers, 63 parts (0 on the bottom side), 67 nets, no tracks yet.

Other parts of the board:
BDC_Out_Screw: BDC_Motor_Screw_Terminal; 01x03_Screw_Terminal
XT60: XT60_Port; AMASS_XT60-F_1x02_P7.20mm_Vertical

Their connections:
/12V_Bus: XT60.1 (12V_raw); also elsewhere on the board
GND: BDC_Out_Screw.3 (GND), XT60.2 (GND); also elsewhere on the board
unnamed 30: BDC_Out_Screw.1 (M+); also elsewhere on the board
unnamed 31: BDC_Out_Screw.2 (M-); also elsewhere on the board

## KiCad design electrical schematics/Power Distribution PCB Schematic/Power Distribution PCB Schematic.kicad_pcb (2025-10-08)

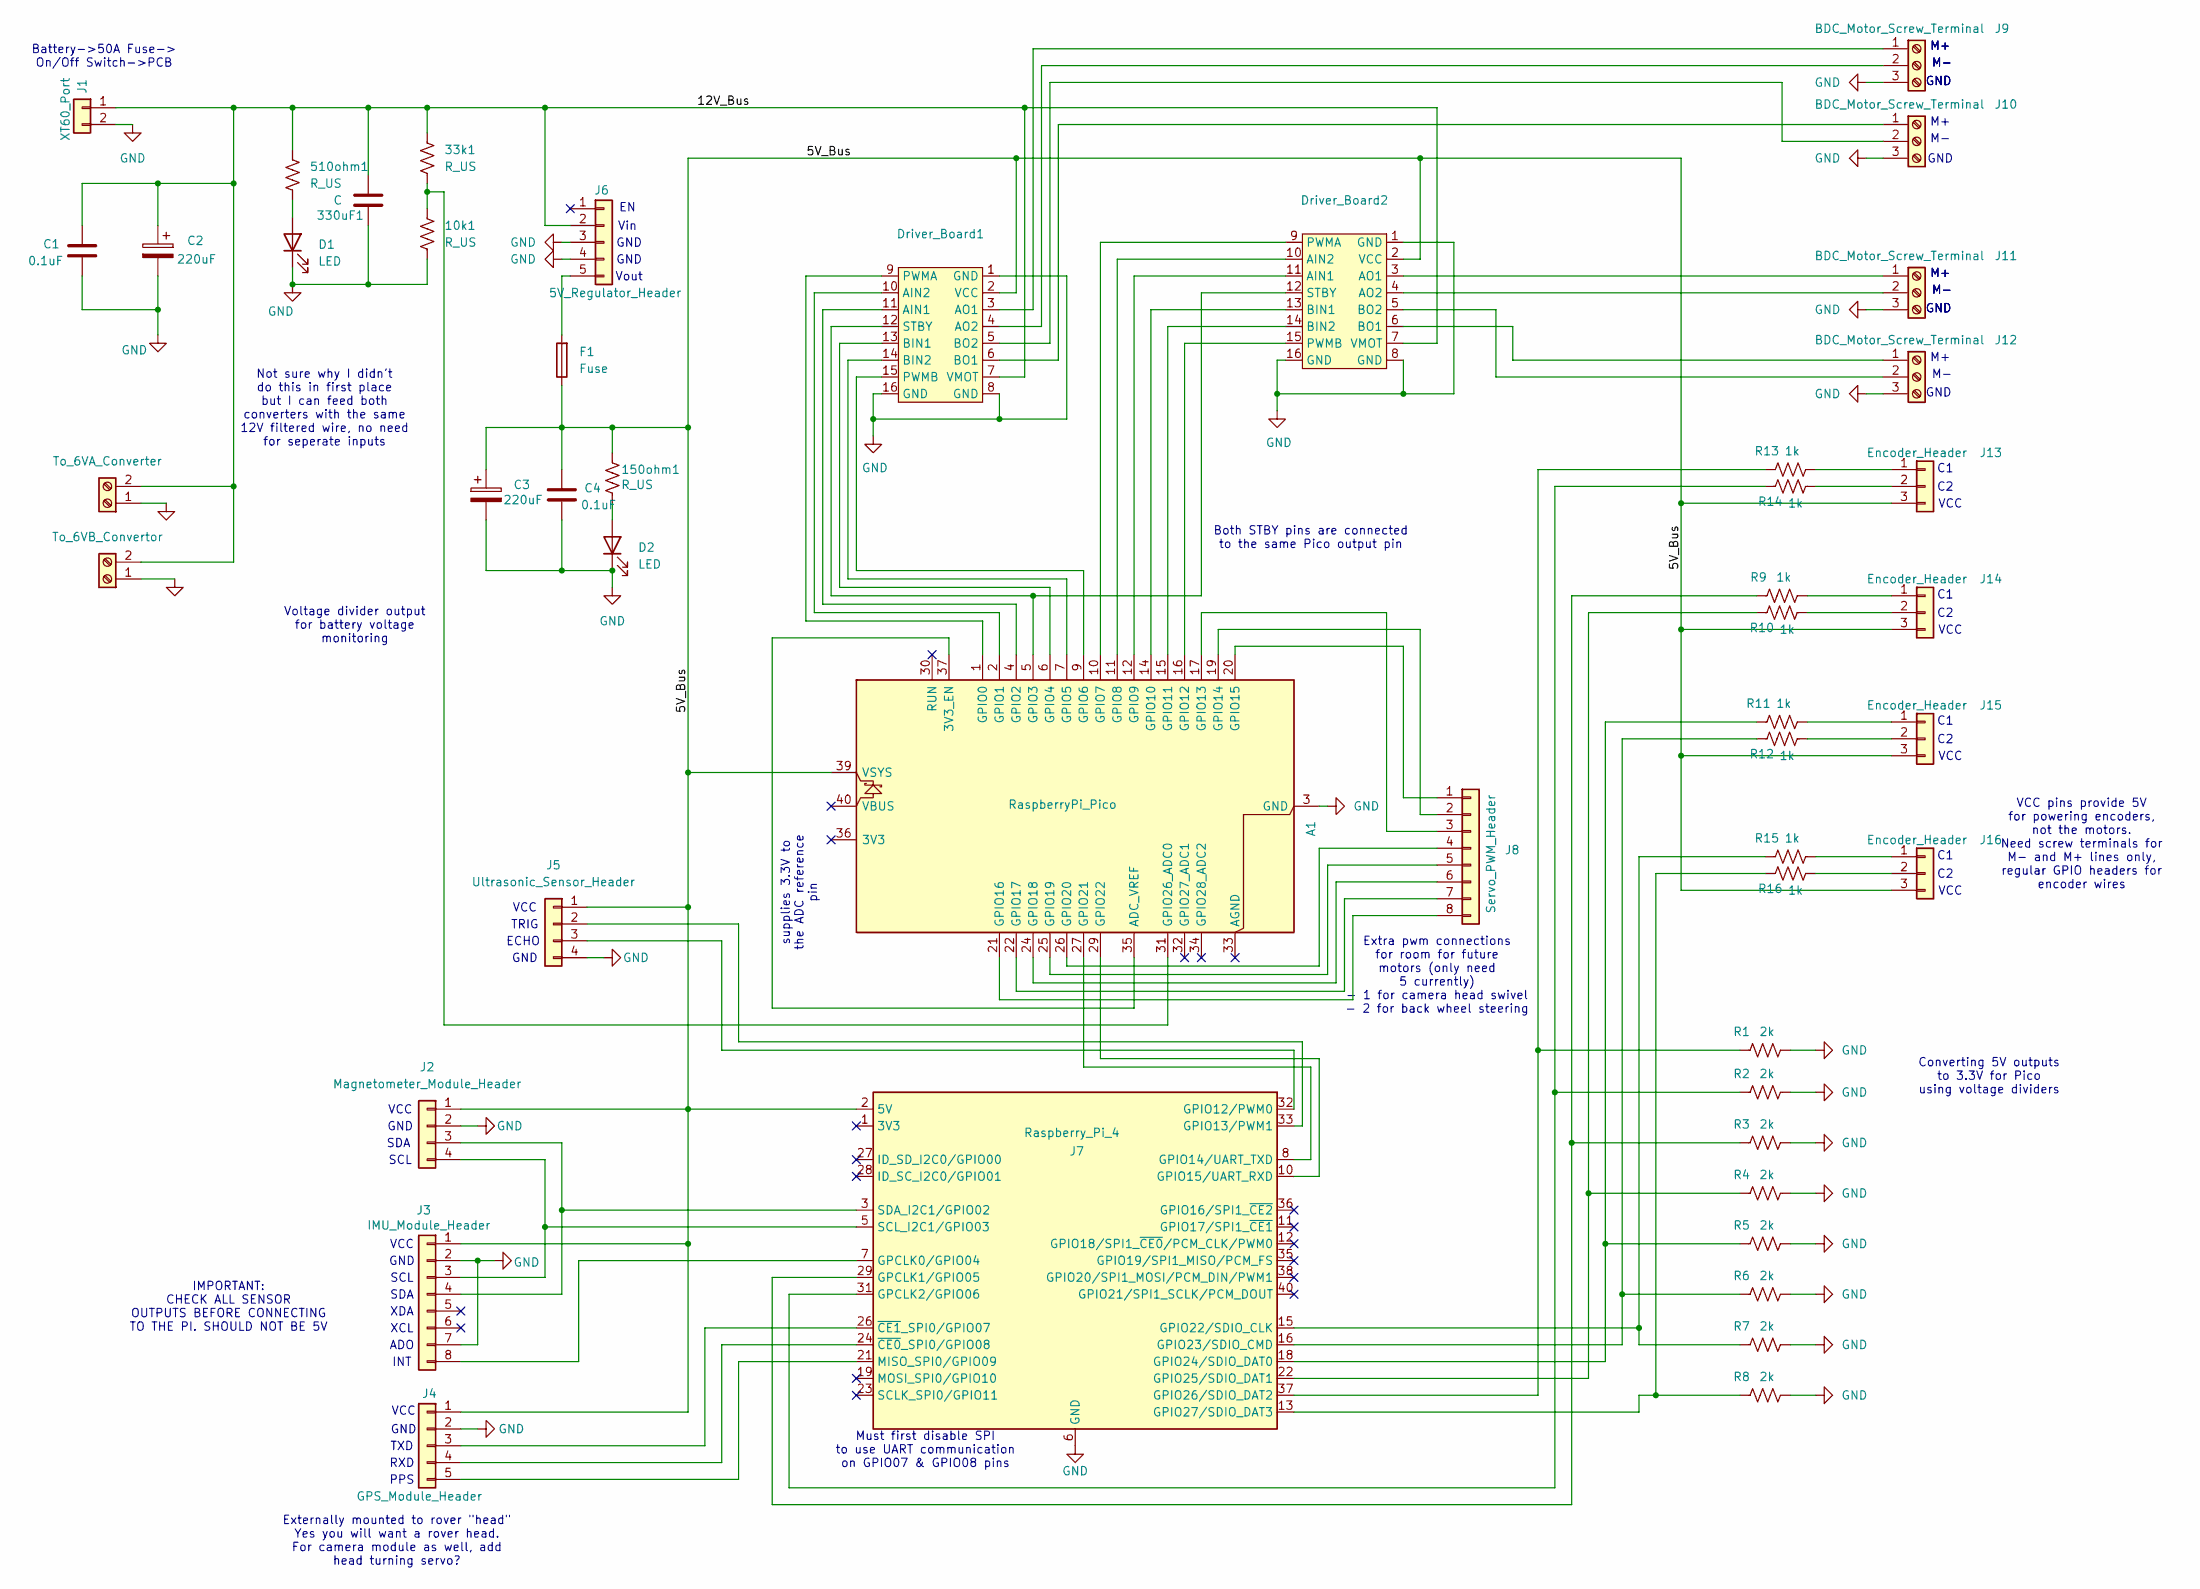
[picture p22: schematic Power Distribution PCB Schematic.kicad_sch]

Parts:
10k1, 33k1, 150ohm1, 510ohm1: R_US; R_Axial_DIN0207_L6.3mm_D2.5mm_P7.62mm_Horizontal
330uF1: C; Ceramic Cap
A1: RaspberryPi_Pico; RaspberryPi_Pico_Common_Unspecified
C1, C4: 0.1uF; Ceramic Cap
C2, C3: 220uF; CP_Radial_D6.3mm_P2.50mm
D1, D2: LED; LED_D3.0mm
Driver_Board1, Driver_Board2: Motor Driver Board
F1: Fuse; Fuse_TH_5A
J1: XT60_Port; AMASS_XT60-F_1x02_P7.20mm_Vertical
J2: Magnetometer_Module_Header; PinHeader_1x04_P2.54mm_Vertical
J3: IMU_Module_Header; PinHeader_1x08_P2.54mm_Vertical
J4: GPS_Module_Header; PinHeader_1x05_P2.54mm_Vertical
J5: Ultrasonic_Sensor_Header; PinHeader_1x04_P2.54mm_Vertical
J6: 5V_Regulator_Header; PinHeader_1x05_P2.54mm_Vertical
J7: Raspberry_Pi_4; SULLINS_PPTC202LFBN-RC
J8: Servo_PWM_Header; PinHeader_1x08_P2.54mm_Vertical
J9, J10, J11, J12: BDC_Motor_Screw_Terminal; 01x03_Screw_Terminal
J13, J14, J15, J16: Encoder_Header; PinHeader_1x03_P2.54mm_Vertical
R1, R2, R3, R4, R5, R6, R7, R8: 2k; R_Axial_DIN0207_L6.3mm_D2.5mm_P7.62mm_Horizontal
R9, R10, R11, R12, R13, R14, R15, R16: 1k; R_Axial_DIN0207_L6.3mm_D2.5mm_P7.62mm_Horizontal
To_6VA_Conv1: To_6VA_Converter; 12AWG Screw Terminal
To_6VB_Conv1: To_6VB_Convertor; 12AWG Screw Terminal

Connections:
/5V_Bus: 150ohm1.1, A1.39 (VSYS), C3.1, C4.1, Driver_Board1.2 (VCC), Driver_Board2.2 (VCC), F1.1, J2.1 (VCC), J3.1, J4.1 (VCC), J5.1 (VCC), J7.2 (5V), J7.4 (5V), J13.3 (VCC), J14.3 (VCC), J15.3 (VCC), J16.3 (VCC)
/12V_Bus: 33k1.2, 330uF1.1, 510ohm1.1, C1.1, C2.1, Driver_Board1.7 (VMOT), Driver_Board2.7 (VMOT), J1.1 (12V_raw), J6.2 (Vin), To_6VA_Conv1.2, To_6VB_Conv1.2
GND: 10k1.2, 330uF1.2, A1.3 (GND), A1.8 (GND), A1.13 (GND), A1.18 (GND), A1.23 (GND), A1.28 (GND), A1.38 (GND), C1.2, C2.2, C3.2, C4.2, D1.2 (K), D2.2 (K), Driver_Board1.1 (GND), Driver_Board1.8 (GND), Driver_Board1.16 (GND), Driver_Board2.1 (GND), Driver_Board2.8 (GND), Driver_Board2.16 (GND), J1.2 (GND), J2.2 (GND), J3.2, J3.7, J4.2 (GND), J5.4 (GND), J6.3 (GND), J6.4 (GND), J7.6 (GND), J7.9 (GND), J7.14 (GND), J7.20 (GND), J7.25 (GND), J7.30 (GND), J7.34 (GND), J7.39 (GND), J9.3 (GND), J10.3 (GND), J11.3 (GND), J12.3 (GND), R1.2, R2.2, R3.2, R4.2, R5.2, R6.2, R7.2, R8.2, To_6VA_Conv1.1, To_6VB_Conv1.1
unnamed: A1.35 (ADC_VREF), A1.37 (3V3_EN)
unnamed: A1.1 (GPIO0), Driver_Board1.9 (PWMA)
unnamed: A1.2 (GPIO1), Driver_Board1.10 (AIN2)
unnamed: A1.4 (GPIO2), Driver_Board1.11 (AIN1)
unnamed: A1.5 (GPIO3), Driver_Board1.12 (STBY), Driver_Board2.12 (STBY)
unnamed: A1.6 (GPIO4), Driver_Board1.13 (BIN1)
unnamed: A1.7 (GPIO5), Driver_Board1.14 (BIN2)
unnamed: A1.9 (GPIO6), Driver_Board1.15 (PWMB)
unnamed: A1.10 (GPIO7), Driver_Board2.9 (PWMA)
unnamed: A1.11 (GPIO8), Driver_Board2.10 (AIN2)
unnamed: A1.12 (GPIO9), Driver_Board2.11 (AIN1)
unnamed: A1.14 (GPIO10), Driver_Board2.13 (BIN1)
unnamed: A1.15 (GPIO11), Driver_Board2.14 (BIN2)
unnamed: A1.16 (GPIO12), Driver_Board2.15 (PWMB)
unnamed: A1.17 (GPIO13), J8.3
unnamed: A1.19 (GPIO14), J8.2
unnamed: A1.20 (GPIO15), J8.1
unnamed: A1.21 (GPIO16), J8.8
unnamed: A1.22 (GPIO17), J8.7
unnamed: A1.24 (GPIO18), J8.6
unnamed: A1.25 (GPIO19), J8.5
unnamed: A1.26 (GPIO20), J8.4
unnamed: A1.27 (GPIO21), J7.8 (GPIO14/UART_TXD)
unnamed: A1.29 (GPIO22), J7.10 (GPIO15/UART_RXD)
unnamed: 10k1.1, 33k1.1, A1.31 (GPIO26_ADC0)
unnamed: 510ohm1.2, D1.1 (A)
unnamed: 150ohm1.2, D2.1 (A)
unnamed: Driver_Board1.3 (AO1), J9.1 (M+)
unnamed: Driver_Board1.4 (AO2), J9.2 (M-)
unnamed: Driver_Board1.6 (BO1), J10.1 (M+)
unnamed: Driver_Board1.5 (BO2), J10.2 (M-)
unnamed: Driver_Board2.3 (AO1), J11.1 (M+)
unnamed: Driver_Board2.4 (AO2), J11.2 (M-)
unnamed: Driver_Board2.6 (BO1), J12.1 (M+)
unnamed: Driver_Board2.5 (BO2), J12.2 (M-)
unnamed: J2.4 (SCL), J3.3, J7.5 (SCL_I2C1/GPIO03)
unnamed: J2.3 (SDA), J3.4, J7.3 (SDA_I2C1/GPIO02)
unnamed: J3.8, J7.7 (GPCLK0/GPIO04)
unnamed: J4.5 (PPS), J7.21 (MISO_SPI0/GPIO09)
unnamed: J4.4 (RXD), J7.24 (~CE0_SPI0/GPIO08)
unnamed: J4.3 (TXD), J7.26 (~CE1_SPI0/GPIO07)
unnamed: J5.3 (Echo), J7.32 (GPIO12/PWM0)
unnamed: J5.2 (Trig), J7.33 (GPIO13/PWM1)
unnamed: F1.2, J6.5 (Vout)
unnamed: J7.29 (GPCLK1/GPIO05), R3.1, R9.1
unnamed: J7.31 (GPCLK2/GPIO06), R2.1, R14.1
unnamed: J7.15 (GPIO22/SDIO_CLK), R7.1, R15.1
unnamed: J7.16 (GPIO23/SDIO_CMD), R6.1, R12.1
unnamed: J7.18 (GPIO24/SDIO_DAT0), R5.1, R11.1
unnamed: J7.22 (GPIO25/SDIO_DAT1), R4.1, R10.1
unnamed: J7.37 (GPIO26/SDIO_DAT2), R1.1, R13.1
unnamed: J7.13 (GPIO27/SDIO_DAT3), R8.1, R16.1
unnamed: J13.1 (C1), R13.2
unnamed: J13.2 (C2), R14.2
unnamed: J14.1 (C1), R9.2
unnamed: J14.2 (C2), R10.2
unnamed: J15.1 (C1), R11.2
unnamed: J15.2 (C2), R12.2
unnamed: J16.1 (C1), R15.2
unnamed: J16.2 (C2), R16.2

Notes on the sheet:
GND
INT
Externally mounted to rover "head" Yes you will want a rover head. For camera module as well, add head turning servo?
GND
TRIG
VCC
Vin
SDA
SCL
supplies 3.3V to the ADC reference pin
TXD
Voltage divider output for battery voltage monitoring
XCL
Battery->50A Fuse-> On/Off Switch->PCB
IMPORTANT: CHECK ALL SENSOR OUTPUTS BEFORE CONNECTING TO THE PI. SHOULD NOT BE 5V
RXD
VCC pins provide 5V for powering encoders, not the motors. Need screw terminals for M- and M+ lines only, regular GPIO headers for encoder wires
Vout
ECHO
PPS
Both STBY pins are connected to the same Pico output pin
Not sure why I didn't do this in first place but I can feed both converters with the same 12V filtered wire, no need for seperate inputs
XDA
Must first disable SPI to use UART communication on GPIO07 & GPIO08 pins
Extra pwm connections for room for future motors (only need 5 currently) - 1 for camera head swivel - 2 for back wheel steering
ADO
Converting 5V outputs to 3.3V for Pico using voltage dividers

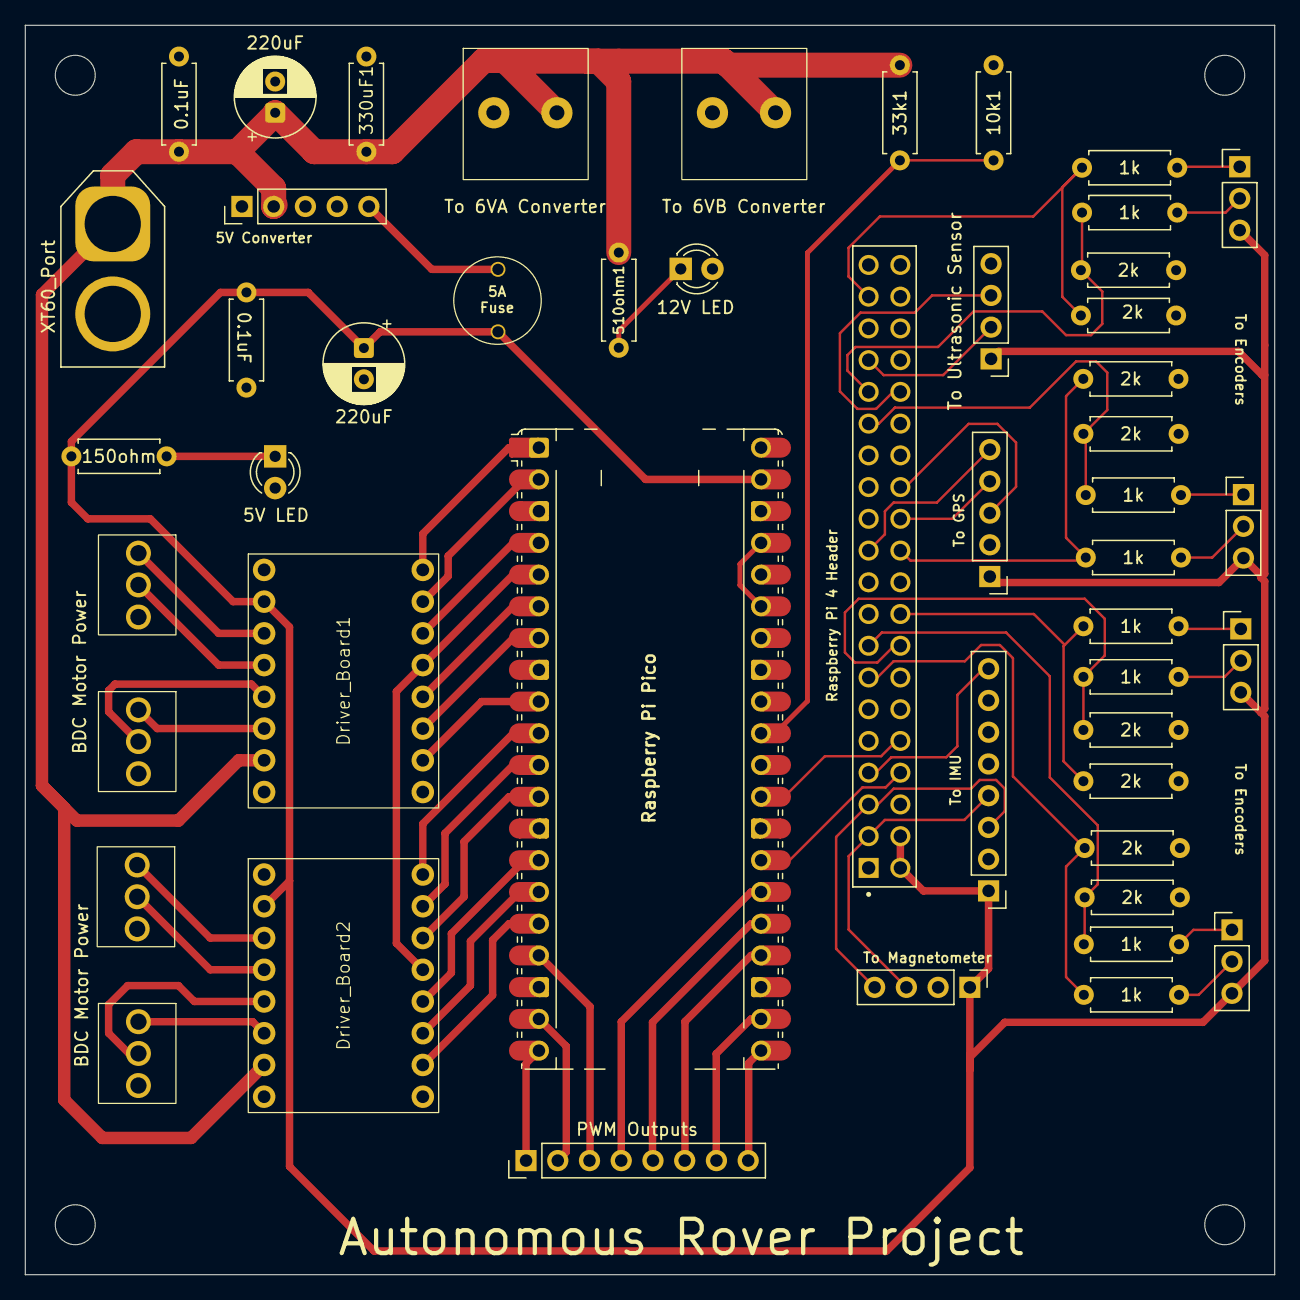
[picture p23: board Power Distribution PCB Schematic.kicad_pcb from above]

Board: 2 copper layers, 100.0 x 100.0 mm, 49 parts (0 on the bottom side), 63 nets.

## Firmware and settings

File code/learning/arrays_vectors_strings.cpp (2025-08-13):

#include <iostream>
#include <vector>
#include <cctype>

using namespace std;

void function_one() { // Managing arrays for storing and accessing data
    const int size = 5;
    int sensor_readings[size];

    // Initializing the arrow
    for (int i = 0; i < size; i++)
        sensor_readings[i] = i * 10;

    // Accessing array elements
    cout << "Sensor Readings: " << endl;
    for (int i = 0; i < size; i++)
        cout << "Sensor " << i + 1 << ": " << sensor_readings[i]  << endl;
}

void function_two() { // Employing vectors for dynamic and resizeable collections
    vector <int> motor_speeds;

    // Adding elements to the vector
    motor_speeds.push_back(100);
    motor_speeds.push_back(200);
    motor_speeds.push_back(150);

    // Accessing vector elements
    cout << "Motor Speeds: " << endl;
    for (int i = 0; i < motor_speeds.size(); i++) {
        cout << "Motor " << i + 1 << ": " << motor_speeds[i] << endl;
    }
}

void function_three() { // Manipulating strings for text handling
    string robot_name = "kwag1227Bot";

    // Accessing a specific char of the string
    cout << "Robot Name: " << robot_name << endl;
    cout << "First Character: " << robot_name[0] << endl;

    // Modifying the string at a specific index
    robot_name[8] = '-';
    cout << "Modified Robot Name: " << robot_name << endl;

    // Merging two strings into one
    string model = "X100";
    string full_name = robot_name + " " + model;
    cout << "Full Name: " << full_name << endl;
}

void function_four() { // Employing character functions for analyzing & processing characters
    char command = 'f';

    // Checking character properties
    if (islower(command))
        cout << "Command is lowercase" << endl;

    // Converting command to upper case
    char uppercase_command = toupper(command);
    cout << "Uppercase Command: " << uppercase_command << endl;

    // Checking character equality
    if (command == 'f')
        cout << "Command is 'f'" << endl;
}

int main() {
    //function_one();
    //function_two();
    //function_three();
    function_four();

    return 0;
}

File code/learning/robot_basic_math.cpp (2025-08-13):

#include <iostream>

using namespace std;

int main () {
    int motor_speed = 100;
    int speed_increment = 20; //Speed adjustment

    int increased_speed = motor_speed + speed_increment; //addition
    int decreased_speed = motor_speed - speed_increment; //subtraction
    int double_speed = motor_speed * 2; //multiplication
    int half_speed = motor_speed / 2; //division
    int remainder = motor_speed % 30; //modulus

    // Output the results
    cout << "Original speed: " << motor_speed << " m/s" << endl;
    cout << "Increased speed: " << increased_speed << " m/s" << endl;
    cout << "Decreased speed: " << decreased_speed << " m/s"  << endl;
    cout << "Doubled speed: " << double_speed << " m/s"  << endl;
    cout << "Halved speed: " << half_speed << " m/s"  << endl; 
    cout << "Remainder: " << remainder << " m/s"  << endl;
    return 0;
}

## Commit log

2025-05-30 Adding master sketch file
    [Master Sketch.SLDPRT]
2025-05-30 Created master sketch
    [Master Sketch.SLDPRT]
2025-06-02 Updating Detailed Block Diagrams
    More accurate description of what is on control PCB board. Also made changes to the roles of the Pi 3 vs Pico. Pico now controls all motor signals and encoder feedback while Pi 3 handles sensor data 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
2025-06-04 Update system block diagrams
    Servos are 5V not 7.4V, will be powered on power distribution PCB 5V bus (high current). Sensors will be powered on control PCB 5V bus (low current).
2025-06-17 Power PCB Circuit Schematic
2025-06-17 Add visible schematic
2025-06-17 Updates to power electrical schematic
2025-06-18 Schematic Work
2025-06-20 Finishing schematics
    Block diagrams are slightly outdated- use schematics instead. (Just need to add 3.3V bus to control pcb + its buck converter and filters.
2025-06-25 Updates to schematics/block diagrams
    Removed 3.3V bus. Added LED resistor values. Removed redundant fuse after 12V-6V converter.
2025-06-25 Organizational changes
    [Master Sketch.SLDPRT]
2025-07-10 Reorganizing
    Mostly electrical file stuff
    [Power Distribution PCB Schematic.kicad_sch]
2025-07-10 Small changes to electrical schematic
    [Power Distribution PCB Schematic.kicad_sch]
2025-07-16 PCB Layout and Schematic Finalization
    [Power Distribution PCB Schematic.kicad_pcb, Power Distribution PCB Schematic.kicad_sch]
2025-07-18 Continued chassis work
    [Ball_Bearing.SLDPRT, Chassis_Subassembly.SLDASM, Corner_Bracket_Subassembly.SLDASM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]
2025-07-21 Electrical System Modifications
    Forgot about the ultrasonic sensor, added to PCB schematic + layout
    [Power Distribution PCB Schematic.kicad_pcb, Power Distribution PCB Schematic.kicad_sch]
2025-07-29 Mechanical Designing
    Finished chassis and began drivetrain
    [Ball_Bearing.SLDPRT, Battery.SLDPRT, Camera Mount Base.SLDPRT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]
2025-07-29 Continued work
    Completely had to reverse the majority of panels because I realized that the differential is supposed to be seated further back on the rover, not towards the front. (I initially messed up the chassis frame). All fixed now besides some of the chassis subassembly fasteners being deleted.
    [Corner_Bracket_Subassembly.SLDASM, Differential Outer Piece.SLDPRT, Master Sketch.SLDPRT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]
2025-07-29 Drivetrain work
    [Corner_Bracket_Subassembly.SLDASM, Differential Center Piece.SLDPRT, Differential Outer Piece.SLDPRT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]
2025-07-30 Drivetrain progress
    [20mm Aluminum Tubes.SLDPRT, Differential Center Piece.SLDPRT, Differential Outer Piece.SLDPRT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]
2025-08-01 Mechanical work
    [20mm Aluminum Tubes.SLDPRT, Bogie Components.SLDPRT, Bogie Joint.SLDASM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]
2025-08-01 Continued design
    [20mm Aluminum Tubes.SLDPRT, Ball_Bearing.SLDPRT, Battery.SLDPRT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]
2025-08-05 PCB Layout Adjustments + Drivetrain Design
    [Bogie Joint.SLDASM, Corner_Bracket_Subassembly.SLDASM, Drive Motor Housing.SLDPRT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]
2025-08-05 Update PCB layout SS
2025-08-06 Drivetrain wheel alignment
    [20mm Aluminum Tubes.SLDPRT, Bogie Components.SLDPRT, Bogie Joint.SLDASM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]
2025-08-06 Middle Wheel Joint Design + Realignment
    [Bogie Components.SLDPRT, Bogie Joint.SLDASM, Corner_Bracket_Subassembly.SLDASM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]
2025-08-07 Top Level Assembly
    [Bogie Components.SLDPRT, Bogie Joint.SLDASM, Corner_Bracket_Subassembly.SLDASM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]
2025-08-07 Wheel tread adjustment
    [Wheel Assembly.SLDASM]
2025-08-11 CAD Finalization
    [Bogie Components.SLDPRT, Bogie Joint.SLDASM, Camera Mount Base.SLDPRT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]
2025-09-27 Print File Creation
    [20mm Aluminum Tubes.SLDPRT, Back Panel.3mf, Back Panel.STL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]
2025-10-08 PCB Schematic v2
    [Power Distribution PCB Schematic-B_Mask.gbr, Power Distribution PCB Schematic-B_Paste.gbr, Power Distribution PCB Schematic-B_Silkscreen.gbr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]
2025-10-08 Schematic SS updating
